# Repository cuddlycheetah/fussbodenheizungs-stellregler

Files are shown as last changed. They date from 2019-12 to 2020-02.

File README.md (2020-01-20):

# fussbodenheizungs-stellregler

This is for a very old(1979) mikrotherm valve.

Other parts needed:
- 10x Turn- Potentiometer 500Ohm Bourns 3590S-2-501 ( https://www.ebay.de/itm/312857872342 )
- Nema 17 Stepper 17HS19-2004S1  https://www.ebay.de/itm/392239468853 )
- TB6600 Stepper Controller ( https://www.ebay.de/itm/233264472435 )
- Arduino Mega 2560 (or Uno)

Print everything in PET-G, PLA is not suitable for this(because its literally melting there)!
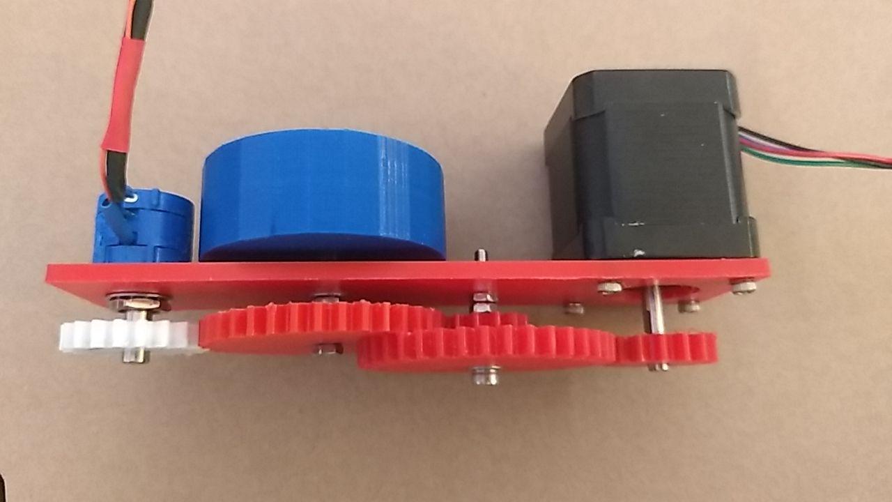
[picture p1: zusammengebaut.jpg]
zusammengebaut

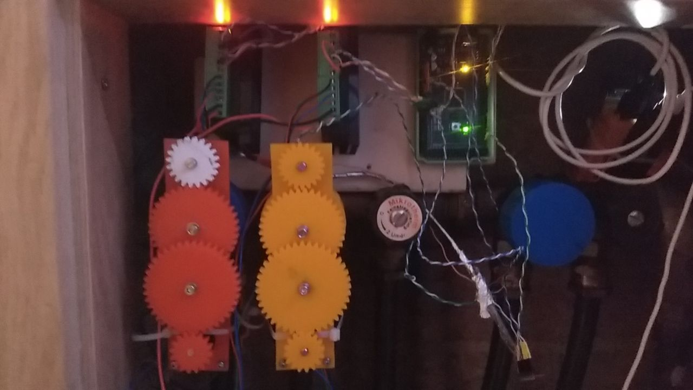
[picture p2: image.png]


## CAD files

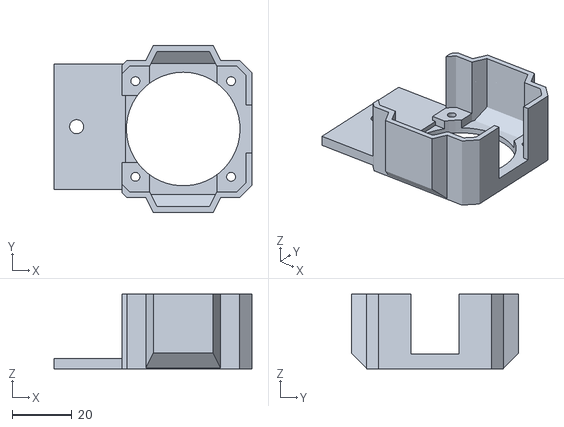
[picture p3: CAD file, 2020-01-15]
Stepperhalter.stl
66.3 x 56.0 x 25.0

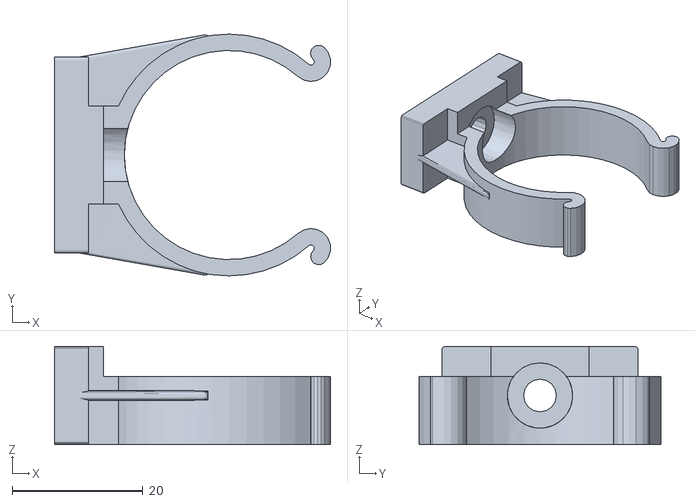
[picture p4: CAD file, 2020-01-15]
Rohrclip.stl
42.2 x 37.0 x 15.0

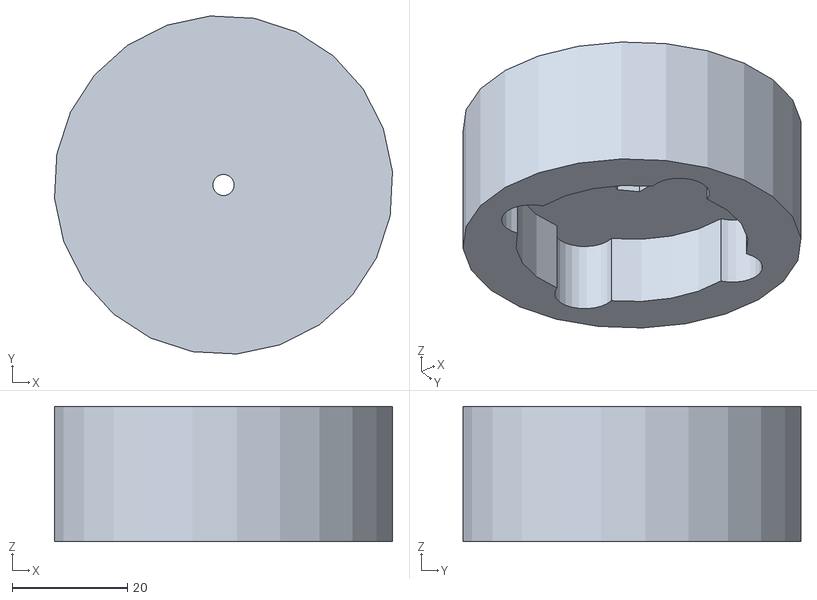
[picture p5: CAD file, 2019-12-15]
Fußbodenheizung-Regler.stl
58.8 x 58.8 x 23.5

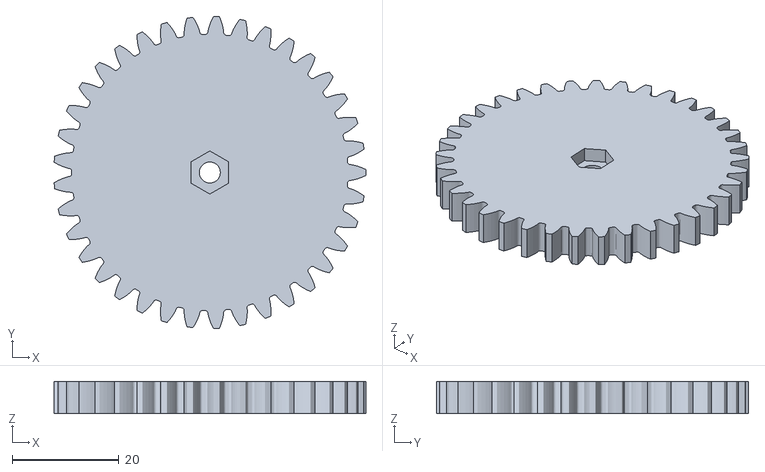
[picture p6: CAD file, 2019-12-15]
gear_regler.stl
58.4 x 58.5 x 6.00

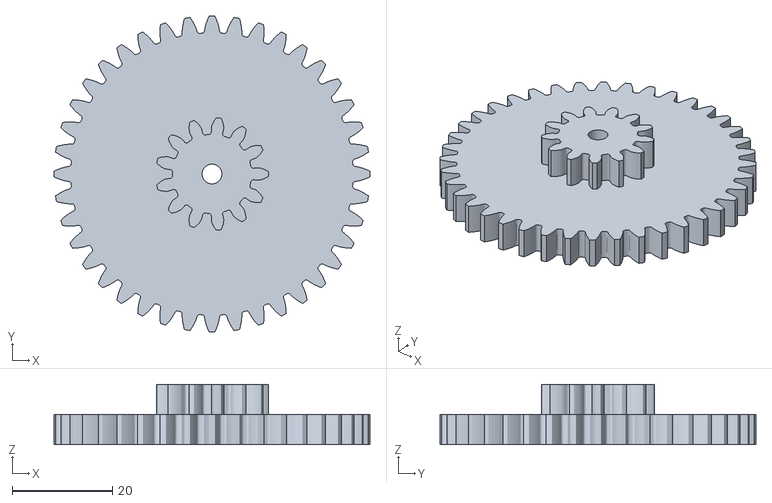
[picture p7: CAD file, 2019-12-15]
gear_middle_new.stl
63.0 x 63.0 x 12.0

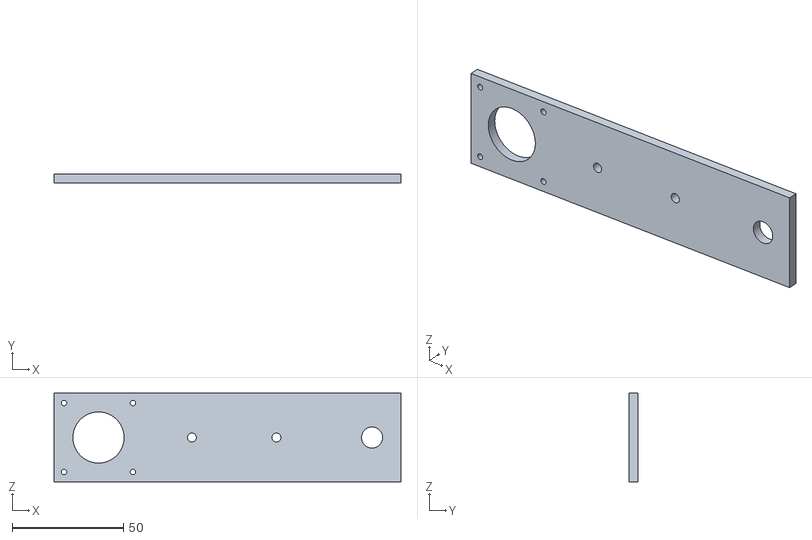
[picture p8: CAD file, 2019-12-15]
BASE_V3_mit POTI.stl
156.0 x 4.00 x 40.0

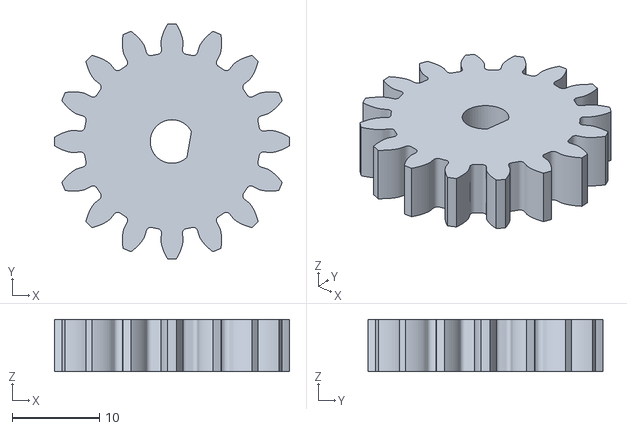
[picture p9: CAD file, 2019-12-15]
gear_stepper.stl
27.0 x 27.0 x 6.00

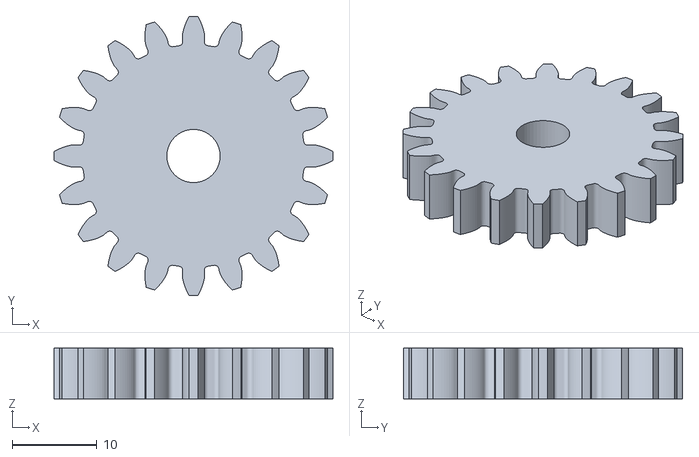
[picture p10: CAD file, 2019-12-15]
GEAR_POTI_Spur Gear (20 teeth).stl
33.0 x 33.0 x 6.00

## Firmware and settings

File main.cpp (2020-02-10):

#include <Wire.h>
#include <Adafruit_ADS1015.h>

Adafruit_ADS1115 ads;  /* Use this for the 16-bit version */
#define TB6600_MASTER_DIR 8
#define TB6600_MASTER_STEP 9

#define POT_0_MIN 650
#define POT_0_MAX 1650
#define TB6600_0_ENABLE 12

#define POT_1_MIN 0
#define POT_1_MAX 1300 //113544
#define TB6600_1_ENABLE 10

#define D_SPEED_FAST 8000

void setup() {
  while (!Serial);
  Serial.begin(230400);
  pinMode(13, OUTPUT);

  pinMode(TB6600_MASTER_DIR, OUTPUT);
  pinMode(TB6600_MASTER_STEP, OUTPUT);
  pinMode(TB6600_0_ENABLE, OUTPUT);
  pinMode(TB6600_1_ENABLE, OUTPUT);
  delay(100);

  tone(TB6600_0_ENABLE, 500);
  delay(200);
  noTone(TB6600_0_ENABLE); 

  digitalWrite(TB6600_0_ENABLE, LOW);
  digitalWrite(TB6600_1_ENABLE, LOW);

  initADC();
}

int32_t ADC0[5] =  { 0x0000, 0x0000, 0x0000, 0x0000, 0x0000 };
int32_t ADC0S;
int32_t ADC1[5] =  { 0x0000, 0x0000, 0x0000, 0x0000, 0x0000 };
int32_t ADC1S;

int potProzent = 0;

void initADC() {
  ads.begin();
  //                                                             ADS1015  ADS1115
  //                                                             -------  -------
  ads.setGain(GAIN_TWOTHIRDS);  // 2/3x gain   +/- 6.144V  1 bit = 3mV      0.1875mV (default)
  //ads.setGain(GAIN_ONE);        // 1x gain   +/- 4.096V  1 bit = 2mV      0.125mV
  //ads.setGain(GAIN_TWO);        // 2x gain   +/- 2.048V  1 bit = 1mV      0.0625mV
  //ads.setGain(GAIN_FOUR);       // 4x gain   +/- 1.024V  1 bit = 0.5mV    0.03125mV
  //ads.setGain(GAIN_EIGHT);      // 8x gain   +/- 0.512V  1 bit = 0.25mV   0.015625mV
  //ads.setGain(GAIN_SIXTEEN);    // 16x gain  +/- 0.256V  1 bit = 0.125mV  0.0078125mV
  initADC0();
  initADC1();
  tone(TB6600_0_ENABLE, 600);
  delay(200);
  noTone(TB6600_0_ENABLE); 
  tone(TB6600_1_ENABLE, 400);
  delay(200);
  noTone(TB6600_1_ENABLE); 

  digitalWrite(TB6600_0_ENABLE, LOW);
  digitalWrite(TB6600_1_ENABLE, LOW);


}
void startProtectedMode() {
  while (true) {
    Serial.println(F("F#FATAL_ADC_FAIL"));
    yield;
    delay(1000);
    tone(TB6600_0_ENABLE, 500);
    delay(500);
    noTone(TB6600_0_ENABLE);
    digitalWrite(TB6600_0_ENABLE, LOW);
  }
}
void initADC0() {
  int16_t val = ads.readADC_SingleEnded(0);
  ADC0[4] = val;
  ADC0[3] = val;
  ADC0[2] = val;
  ADC0[1] = val;
  ADC0[0] = val;
  ADC0S = val;
  if (val == -1) { Serial.println("ADC not working"); startProtectedMode(); }
  potProzent = map(ADC0S / 10, POT_0_MIN, POT_0_MAX, 0, 1024);
}
void initADC1() {
  int16_t val = ads.readADC_SingleEnded(1);
  ADC1[4] = val;
  ADC1[3] = val;
  ADC1[2] = val;
  ADC1[1] = val;
  ADC1[0] = val;
  ADC1S = val;
  if (val == -1) { Serial.println("ADC not working"); startProtectedMode(); } 
  potProzent = map(ADC1S / 10, POT_1_MIN, POT_1_MAX, 0, 1024);
}
void readADC(int driverId) {
  if (driverId == 0) readADC0();
  if (driverId == 1) readADC1();
}

void readADC0() {
  ADC0[4] = ADC0[3];
  ADC0[3] = ADC0[2];
  ADC0[2] = ADC0[1];
  ADC0[1] = ADC0[0];
  ADC0[0] = ads.readADC_SingleEnded(0);
  ADC0S = (ADC0[0] + ADC0[1] + ADC0[2] + ADC0[3] + ADC0[4]) / 5;
  potProzent = map(ADC0S / 10, POT_0_MIN, POT_0_MAX, 0, 1024);
  if (potProzent > 2048) { Serial.println("ADC not working"); startProtectedMode(); } 
}
void readADC1() {
  ADC1[4] = ADC1[3];
  ADC1[3] = ADC1[2];
  ADC1[2] = ADC1[1];
  ADC1[1] = ADC1[0];
  ADC1[0] = ads.readADC_SingleEnded(1);
  ADC1S = (ADC1[0] + ADC1[1] + ADC1[2] + ADC1[3] + ADC1[4]) / 5;
  potProzent = map(ADC1S / 10, POT_1_MIN, POT_1_MAX, 0, 1024);
  if (potProzent > 2048) { Serial.println("ADC not working"); startProtectedMode(); } 
}

void gotoTarget(int target, int driverId) {
  digitalWrite(TB6600_0_ENABLE, driverId == 0);
  digitalWrite(TB6600_1_ENABLE, driverId == 1);
  double t = 800;
  int i = 0;
  int turnOvers = 0;
  bool lastDirection = 0;
  long steps = 0;

  readADC(driverId);
  int startProzent = potProzent + 0;
  long startMillis = millis();

  while ( abs(potProzent - target) >= 1) {
    boolean nowDirection = (potProzent - target) > 0;
    if (millis() - startMillis > 30 * 1000) break; 

    if (nowDirection != lastDirection) turnOvers++;

    t = map( abs(potProzent - target), 0, 200, 1, 300);
    t = t > 30 ? D_SPEED_FAST : 20;
    t = floor(t/2) * 2;
    steps++;

    // rotate 1 step
    digitalWrite(TB6600_MASTER_DIR, nowDirection);
    digitalWrite(TB6600_MASTER_STEP, HIGH);
    delay(45); //delayMicroseconds(1000000 / t);
    digitalWrite(TB6600_MASTER_STEP, LOW);
    delay(50); //delayMicroseconds(1000000 / t);
    // read results sometimes
    if ((t > 50 && i % 50 == 0) || (t <= 50 && i % 10 == 0)) {
      readADC(driverId);
    }
    i++;

    lastDirection = nowDirection;

    if (turnOvers > 3) {
      Serial.println("F#MAXCORRECTIONS");
      break;
    }
  }
  digitalWrite(TB6600_0_ENABLE, LOW);
  digitalWrite(TB6600_1_ENABLE, LOW);
}

void loop() {
  readADC0();
  Serial.print('A');
  Serial.println(potProzent);
  readADC1();
  Serial.print('B');
  Serial.println(potProzent);

  if (Serial.available() > 0) {
    String line = Serial.readString();
    if (line.indexOf('#') > -1) {
      String command = line.substring(0, line.indexOf('#'));
      String args = line.substring(line.indexOf('#') + 1);
      // set cmd
      if (command.equalsIgnoreCase(F("A")) || command.equalsIgnoreCase(F("B"))) {
        String arg0 = args.substring(0, args.indexOf('#'));
        String arg1 = args.substring(args.indexOf('#') + 1);
        if (atoi(arg0.c_str()) != 1000 - atoi(arg1.c_str()))  {
          Serial.println(F("F#CHECKSUM"));
          return;
        }
        if (ads.readADC_SingleEnded(0) == -1) { Serial.println("ADC not working"); startProtectedMode(); }
 
        int rotation = atoi( arg0.c_str() );
        rotation = min(max(rotation, 0), 1000);
        if (command.equalsIgnoreCase(F("A"))) gotoTarget(rotation, 0);
        if (command.equalsIgnoreCase(F("B"))) gotoTarget(rotation, 1);
      }
      // debug cmd
      if (command.equalsIgnoreCase(F("D"))) {
        Serial.print("D#millis"); Serial.println(millis());
        Serial.print("D#adc0"); Serial.println(ADC0S);
        Serial.print("D#adc1"); Serial.println(ADC1S);
      }
    }
  }
  delay(50 * 1);
}

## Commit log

2019-12-15 Files for building the hardware
    [BASE_V3_mit POTI.stl, GEAR_POTI_Spur Gear (20 teeth).stl, gear_middle_new.stl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]
2019-12-25 updated firmware
    + support for dual valves.
    + failure detection when not reaching target value(F#MAXCORRECTIONS)
    + added "checksum" for preventing wrong values being set by serial errors
    [main.cpp]
2020-01-15 added some misc files for the case someone needs them
    [Rohrclip.stl, Stepperhalter.stl]
2020-02-10 Silent Mode
    slowed the motor down to prevent noise
    [main.cpp]
